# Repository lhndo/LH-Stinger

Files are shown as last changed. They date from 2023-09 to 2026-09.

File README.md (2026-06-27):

<p align="center">
  <p align="center">
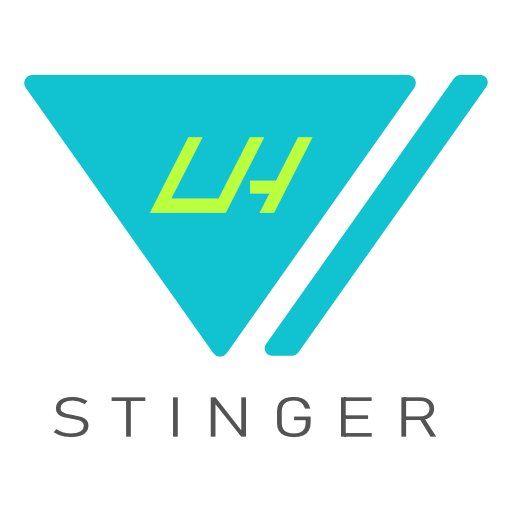
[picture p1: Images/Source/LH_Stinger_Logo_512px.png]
   
  </p>
	<h1 align="center"><b>LH Stinger</b></h1>
	<p align="center"> <strong>
		A no-compromise cartesian 3D Printer designed for speed and precision, created as a long-lasting platform for those who like to push quality and speed to the extreme.  </strong>
    <br />
    <br />
        <br />
    <i>~ A community-driven project ~ </i>
    <br /> 
    <br />
      
    <br />
</a>
  </p>
</p>

<br>

Image of LH Stinger 3D Printer Front View  

<br>

  
Status: **V1.0**  

<br>

## Sponsors

JLCPCB (https://flexheater.jlcpcb.com/?from=LH_STINGER)
  
   Sponsored by [JLCPCB Flexible Heaters](https://flexheater.jlcpcb.com/?from=LH_STINGER) - **Custom Flex Heaters for Your Build**
<br>

## Contents

- [Features](#features)
- [Kits - BOM](#kits---bom)
- [Resources](#resources)
- [Assembly Instructions](#assembly-instructions)
- [Addons](#addons)
- [Contact](#contact)
- [Credits](#credits)
- [Supporters](#supporters)
- [License](#license)

<br>

## Features
_**(at BOM Spec)**_
<br>

- Cross Frame design focused on stiffness and stability with a low center of gravity
- Streamlined frame assembly consisting of only six extrusions
- Lightweight bed carriage assembly with carbon fiber components
- AWD stepper configuration for the Y-axis
  - Optional conversion for X-axis AWD setup
- 235 x 235 x 200 mm maximum build volume (easily expandable to other sizes)
  - (200 mm)^2 [Carbon Fiber Bed](/DXF) for high-speed setup
  - (235 mm)^2 bed support for a larger volume
- Optimized for daily print speeds of 400-600 mm/s with 20.000 mm/s^2 acceleration ([Test A](https://www.youtube.com/watch?v=bxNQv3xVFXA&)) ([Test B](https://www.youtube.com/watch?v=mh0rmYptH-0)) ([Test C](https://www.youtube.com/watch?v=cDipS-Msi5c))
- Motion system capable of 1.000 mm/s speed with 100.000 mm/s^2 acceleration ([Test](https://www.youtube.com/watch?v=Xajs2mky6ZU))
- Maximum volumetric flow rate: ~55-60 mm^3/s ([Test A](https://www.youtube.com/watch?v=K3M1EXKJzKs)) ([Test B](https://www.youtube.com/shorts/JorOoNuft90))
- Built using 30 series T-slotted extrusions with parts up to 3090
- All bracket assembly
- Genuine high-quality motion system components ([BOM](https://docs.google.com/spreadsheets/d/1s8ulLfThmbuy1G_40MvkXXL2oVx9PZhvpAY9hMxqYbg/edit?usp=drive_link))
- Entire motion system based on high preload MGN12H linear guide rails
- Fully belt-driven with minimal belt paths
- 9mm 2GT belt in symmetrical configuration for the Y-axis
- 6mm 2GT belts for the rest of the axis
- Independent Z stepper motors with Z Tilt capability for the X-axis
- Lightweight dual plate [Carbon Fiber Bed Carriage](/DXF) with integrated tensioner and compatible with different bed sizes and carriage configurations
- Rigid carbon fiber bed mount
- Lightweight Polyimide flex PCB 200W [Bed Heater](/PCB/PI%20Bed%20Heater%20-%20200mm)
- Double shear shaft supports for Y and X axis steppers
- High torque LDO-42STH48-2504AC stepper motors supplied with 36V for the X and Y-axis
- Dual power supply supporting 24V and 36V power standards (easily configurable for 48V)
- Driven by the Octopus Pro 1.1 board with TMC2240 drivers
- Running [Klipper](https://github.com/Klipper3d/klipper)/[Kalico](https://github.com/KalicoCrew/kalico) firmware
- Fully featured Klipper [Configuration](/Config/Klipper_Config) and [Slicer Profiles](/Config/Klipper_Config#slicers) available
- Easily serviceable [External electronic box](https://github.com/lhndo/LH-Stinger/wiki/Build-Log#electronic-box-design) with good airflow, and support for multiple power supplies, SSRs, RPi and large controller boards.
- Good cable management with a quick disconnect [Breakout Board](/PCB/LHS%20Breakbeat) between the printer and ebox
- Toolhead based on the Dragon HF hotend and HF extender
  - Alternate hotends supported: Dragon UHF, Ace, Mellow NF-Crazy-Volcano HF, Rapido, Goliath ([User Mods](/User_Mods/Toolhead/))
- LDO Orbiter 2.5 direct drive extruder
  - Sherpa Mini supported ([User Mods](/User_Mods/Printer))
- Dual 5015 fan setup for part cooling
- Dual [AUX cooling modules](/CAD/Aux%20Fan) based on 9733 blower fans providing 64 CFM of auxiliary cooling
- Adopts the [Annex Engineering Quickdraw Probe](https://github.com/Annex-Engineering/Quickdraw_Probe)
	- Zero Y offset probe placement for no gantry twist deviation
	- Full bed probe coverage
- Minimalistic [printed part design](/STL) focused on strength and easy printability
- Printed in ASA, providing high temperature resistance
- Easily enclosed, with the main electronic components outside of the build chamber.
  - The (200 mm)^2 bed configuration can be fully enclose up to the frame bounding box, with no extra space needed for the bed movement. ([Dimensions](https://github.com/lhndo/LH-Stinger/wiki/Dimensions))

<br>

**Resonance Tests:**<br>
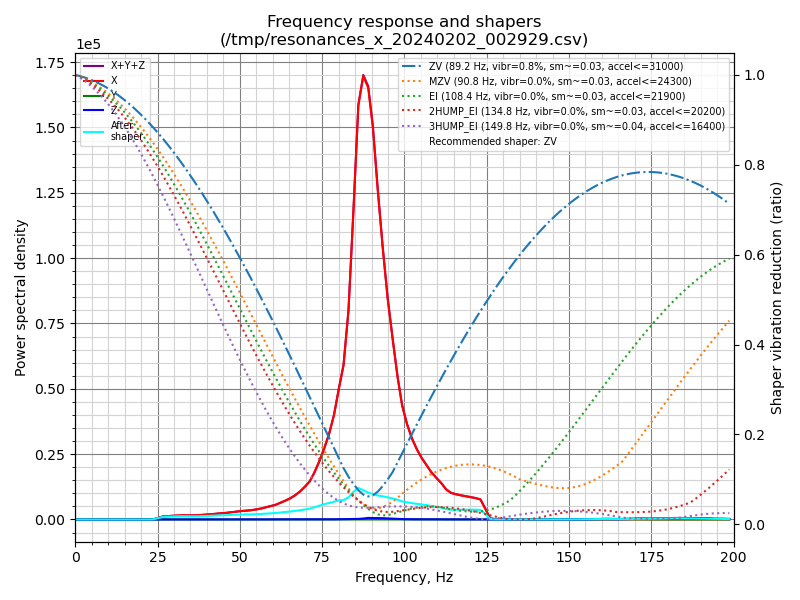
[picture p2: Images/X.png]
Resonance Test X
<br>
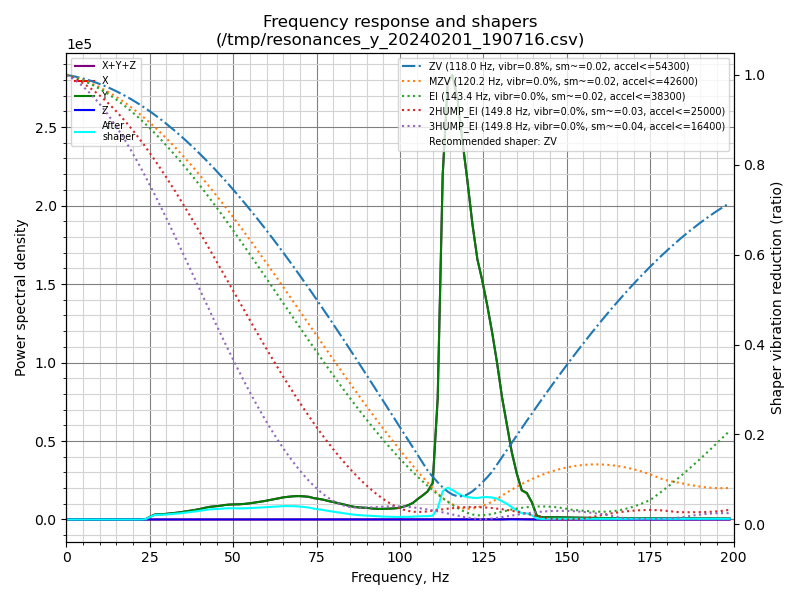
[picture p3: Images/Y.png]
Resonance Test Y
<br>

<br>

## Kits - BOM

* This project can be self-sourced by following the [**BOM Guide**](https://docs.google.com/spreadsheets/d/1s8ulLfThmbuy1G_40MvkXXL2oVx9PZhvpAY9hMxqYbg/).  

* An official upgraded **LH Stinger - Rev2 Kit** is produced and sold by **[FYSETC](https://www.fysetc.com/products/lh-stinger-3d-printer-kit)**.

Fysetc LH Stinger Rev2 Kit (https://www.fysetc.com/products/lh-stinger-3d-printer-kit)<br>

### Kit Highlights:

* Phaetus Dragon UHF - Hotend
* FYSETC Sherpa Mini - All Metal - CNC Extruder
* MGN 12H Z1 Preload Linear Rails
* FYSETC Spider V3.0 H7 (550Mhz) High Voltage board 
* 48V Power with TMC5160 Drivers (AWD Y, X Axis)
* High Torque 2.5A 580mN.m Stepper Motors with 30mm shafts for double shear support
* Delta (48V) and Meanwell (24V) PSUs
* Carbon Fiber Bed with Pre-applied PI Heater and Pre-epoxied CF Carriage Assembly
* LHS Breakbeat distribution board and wiring harness

**You require**: The **Printed Parts** and a **BTT Pi V1.2** or **Raspberry Pi** SBC (Klipper Host)
<br>

[**Fysetc - LH Stinger - Kit**](https://www.fysetc.com/products/lh-stinger-3d-printer-kit)  
  
Use the code **FYSBKSALELH** for a total of **$699**. Free shipping directly from US/EU.  
A portion of every kit sale goes towards supporting the project! :purple_heart:  

<br>

## Resources
<br>

- [**Assembly Guide**](https://github.com/lhndo/LH-Stinger/wiki/)
- [STL Files and Printing Instructions](STL/)  
- [CAD Source Files ](CAD/)
- [Klipper Configuration ](Config/Klipper_Config) 
- [Build Log](https://github.com/lhndo/LH-Stinger/wiki/Build-Log)
- [Videos](https://www.youtube.com/channel/UCPD2Ai4b49gVoCFSGFWoSdw) 

<br>

## Assembly Instructions 

* The [LH Stinger Wiki](https://github.com/lhndo/LH-Stinger/wiki) is a regularly updated and intended to serve as your primary point of reference during the build  

* The main body of documentation can be found in the [**Assembly Guide**](https://github.com/lhndo/LH-Stinger/wiki/Assembly-Guide)  

<br>

*For additional support please join us on the [LH Stinger Discord](https://discord.gg/EzssCfnEDS)*

<br>

## Addons

- [**LHS Pico MMU**](https://github.com/lhndo/LH-Stinger/wiki/Pico-MMU)  

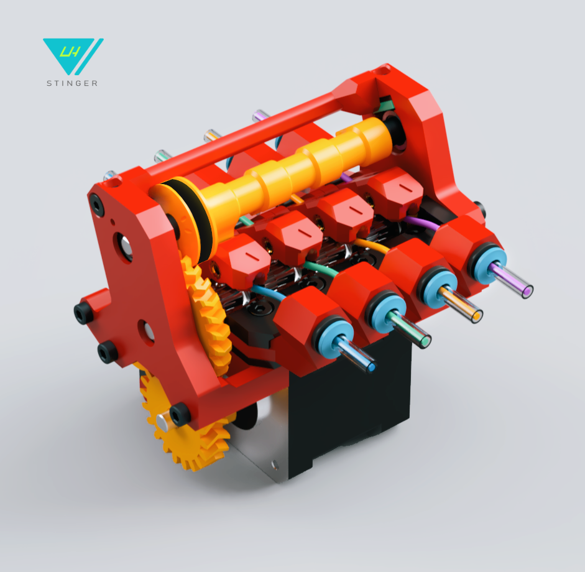
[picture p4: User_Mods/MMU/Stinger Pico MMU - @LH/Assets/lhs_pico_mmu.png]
LH Stinger - LHS - Pico MMU


- **Enclosure** *(In progress)* 
  *by zwirbel*

<br>

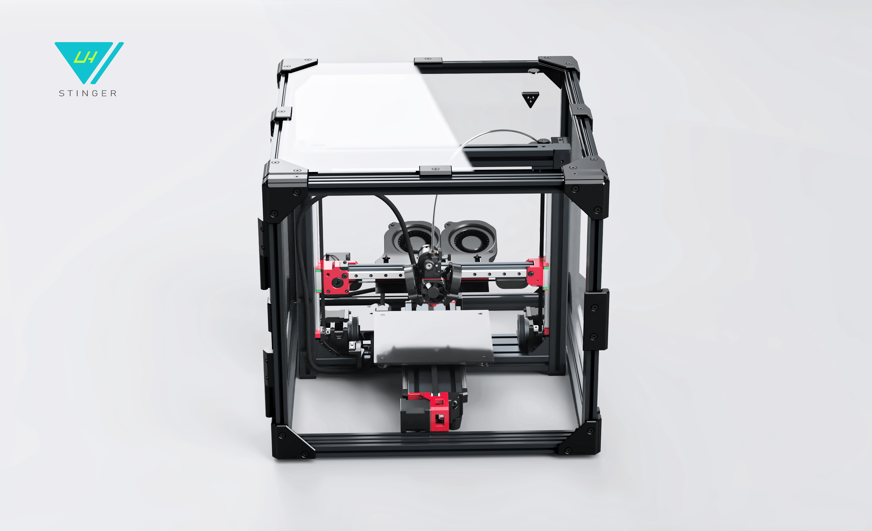
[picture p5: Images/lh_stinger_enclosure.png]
LH Stinger Enclosure
  

<br>

- An extensive range of [**community mods**]((/User_Mods)) available

<br>

## Contact

lemurshaze @ gmail.com  
@LH on [LH Stinger Discord](https://discord.gg/EzssCfnEDS)
<br>

## Credits

<br>

**Thanks to everyone in the LH Stinger community who supported the project, contributed in any form, or provided feedback! :purple_heart:**

<br>

_Inspired by the [Annex Engineering](https://github.com/Annex-Engineering) team and [community](https://discord.com/invite/MzTR3zE), along with the [Klipper community](https://discord.klipper3d.org), [RatRig](https://ratrig.com/) and all the crazy people that continue to push bed slingers to their limits. :purple_heart:_

-Toolhead evolved from an amazing design by [Dalegaard](https://github.com/dalegaard)  
-Silicon sock mold based on [Renátó Kulman](https://www.printables.com/@RenatoKulman)  
-Wago 221 mounts by [fns720](https://www.printables.com/@fns720)  
-SSR protection cover based on [Technoturk](https://www.printables.com/@Technoturk_377911)  
-3030 extrusion Cable clip based on [Arthur_C](https://www.printables.com/@Arthur_C_428094)  
-3030 t-nut clip based on [John_S](https://www.printables.com/@JohnS)  
<br>

## Supporters

<br>

*Special thanks to those who donated to this project throughout its development!* :purple_heart:  

**djezo888. Fen, Budz, techb0i, PinGZ, abstractFlo, BeccaK, Steven @crydteam, Robin @crydteam, Fred Bernton, Mawoka, rmxbit, Mcclane, malar6606, EMMY BEAR 3D, Killa_Prints, Michel, vr6deezy, Ajax240, Zemlos01, popster, Dan, Sibert, Ultracopa, yoske, Arjun, iKuro**  

If you would like to give your support, please use the link below:



<br>

## License

This work is licensed under a [Creative Commons (4.0 International License)  ](https://creativecommons.org/licenses/by-nc-sa/4.0/)  
[**Attribution—Noncommercial—Share Alike**](LICENSE.md)  

[][cc-by-nc-sa] [][l2] [][l5] 

[s1]: https://img.shields.io/badge/Buy%20Me%20a%20Coffeee-d3dsds?logo=ko-fi&logoColor=white&labelColor=red&color=red
[l1]: https://ko-fi.com/lh_eng
[s2]: https://img.shields.io/badge/Discord-asdsadsa?logo=discord&logoColor=white&color=5865F2
[l2]: https://discord.gg/EzssCfnEDS
[s5]: https://img.shields.io/badge/Youtube-8A2323443?logo=youtube&logoColor=red&color=white
[l5]: https://www.youtube.com/@LemurHaze

[cc-by-nc-sa]: http://creativecommons.org/licenses/by-nc-sa/4.0/
[cc-by-nc-sa-image]: https://licensebuttons.net/l/by-nc-sa/4.0/88x31.png
[cc-by-nc-sa-shield]: https://img.shields.io/badge/License-CC%20BY--NC--SA%204.0-lightgrey.svg

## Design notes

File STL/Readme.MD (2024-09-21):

[:arrow_double_down: Download Folder](https://download-directory.github.io/?url=https%3A%2F%2Fgithub.com%2Flhndo%2FLH-Stinger%2Ftree%2Fmain%2FSTL)

## Naming Conventions

Filename Example: **AC** Y Stepper Mount A **SUP x2**.stl

> **AC** - Accent color part  
> **SUP** - Supports needed  
> **x2** - Number of part copies required

<br>

## Print Settings

### Filament Options  
&nbsp;&nbsp;&nbsp;&nbsp; **Printer**: ASA, PC (CF, GF)  
&nbsp;&nbsp;&nbsp;&nbsp;&nbsp;**Ebox, Breakout**:  PETG, ASA, ABS (Flame-retardant Filaments)  

### Slice Setings

&nbsp;**Printer Parts:**  

&nbsp;&nbsp;&nbsp;&nbsp;Nozzle Size: 0.4 or 0.5 mm  
&nbsp;&nbsp;&nbsp;&nbsp;Layer Height: 0.2  
&nbsp;&nbsp;&nbsp;&nbsp;Line Width: 0.4  (0.5mm)  
&nbsp;&nbsp;&nbsp;&nbsp;Perimeters: 4  
&nbsp;&nbsp;&nbsp;&nbsp;Top / Bottom Layers: 6/5  
&nbsp;&nbsp;&nbsp;&nbsp;Infill Density: 40% minimum  
&nbsp;&nbsp;&nbsp;&nbsp;Infill Type: 3D Honeycomb, Gyroid, Cubic 

&nbsp;**Ebox, Breakout, Other Parts:**  
&nbsp;&nbsp;&nbsp;&nbsp;At your discretion  

<br>

>**Note: If printing the STL files individually in another slicer,  please install Orca Slicer and reference the orientation and supports used in the provided ready made 3mf plates.**

<br>

## Filament Amounts

Printer: 260g  
Printer Accents: 210g

Aux Fan: 127g  
Aux Fan Accents: 44g

Breakout: 97g

Ebox: 729g  
Ebox Accents: 49g

Other Parts: 204g  

<br>

## Assemblies

Files containing all the parts organized by plates are available in the .3mf format for [Orca Slicer](https://github.com/SoftFever/OrcaSlicer)

**Printer Parts:**  <br>

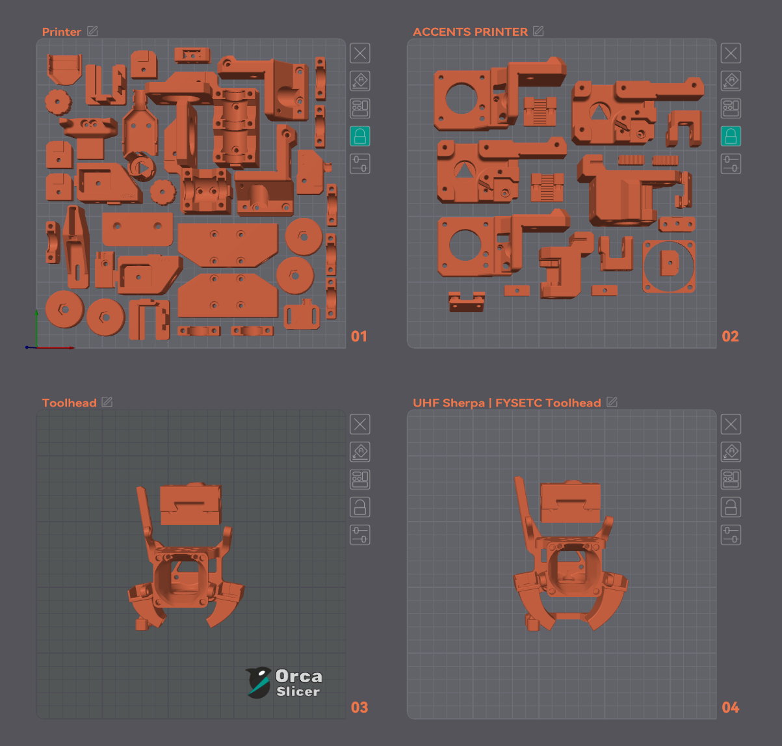
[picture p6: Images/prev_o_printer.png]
  
<br>

**Aux Fan Parts:**  <br>

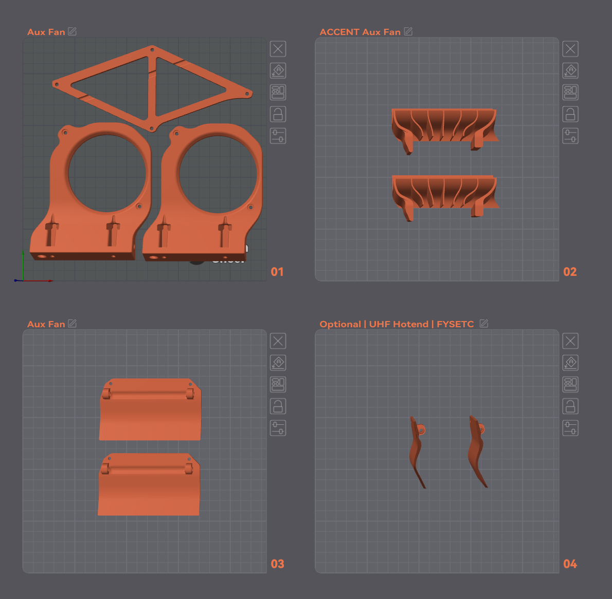
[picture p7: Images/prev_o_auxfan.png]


<br>

**Ebox Parts:**  <br>

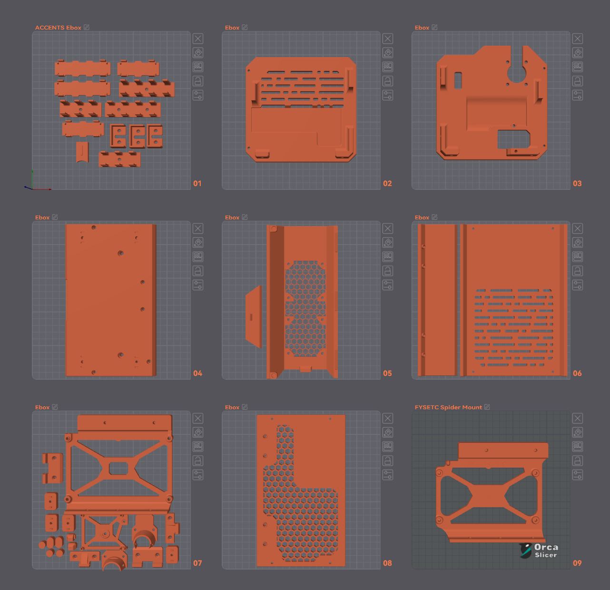
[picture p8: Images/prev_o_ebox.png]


<br>

**Breakout Box Parts:**  <br>

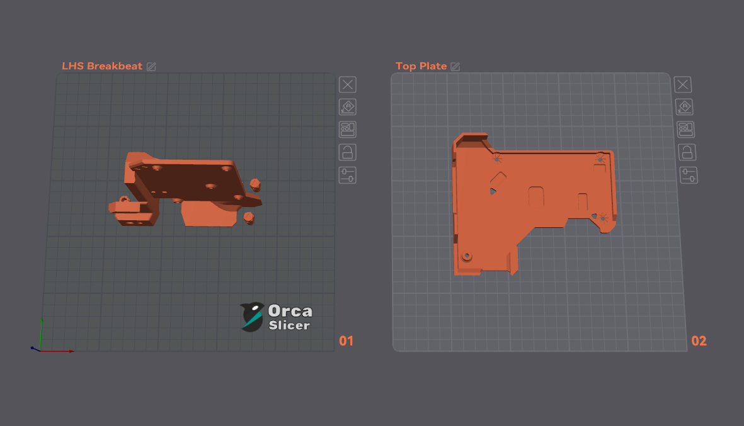
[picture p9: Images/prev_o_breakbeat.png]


<br>

**Other Parts:**  <br>

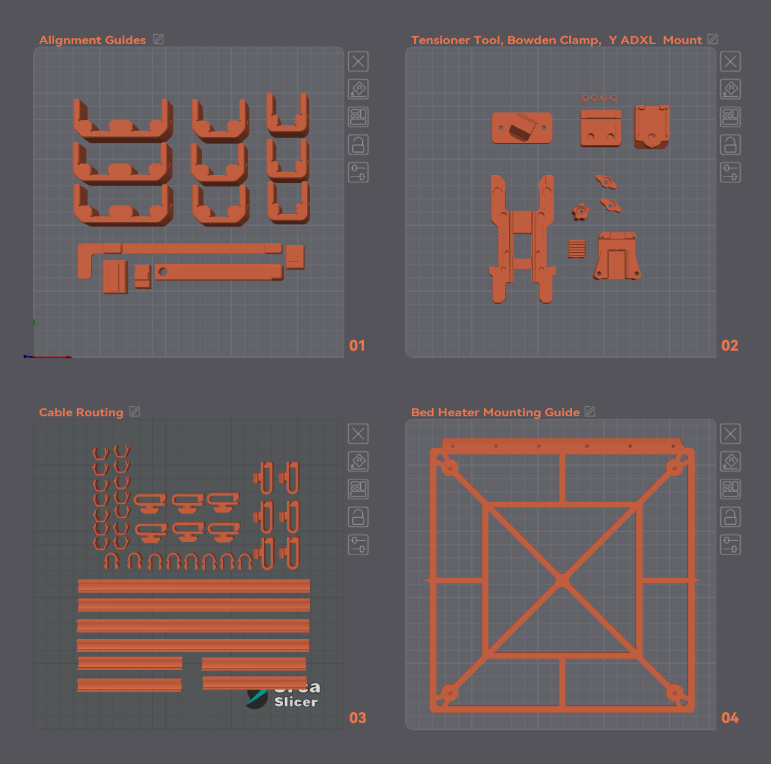
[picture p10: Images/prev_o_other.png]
  
<br>

## Quickdraw

Details about the Quickdraw probe can be found on the [Annex Engineering Git](https://github.com/Annex-Engineering/Quickdraw_Probe/tree/main)  
The file required for building the probe is **omron_d2f-5_microswitch_probe_body_x1_rev3.STL**  
from: https://github.com/Annex-Engineering/Quickdraw_Probe/tree/main/STLs/Release_1

Assembly tips can be found in the [Toolhead Guide - Probe](https://github.com/lhndo/LH-Stinger/wiki/Toolhead#probe) section.  

Note: The dock detection feature is not required and not accounted for in the dock stl.

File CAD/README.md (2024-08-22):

## CAD

The project was built in Fusion 360, and those files are preferred as the primary choice for consulting the assembly.  
They are packed into f3z files, which maintain links/instances to all components and sub-assemblies. This way it is easier to make modifications by third parties and keep track of the changes for future integration.  
It is advised to create a folder inside your Fusion workspace in which to import the f3z.  
<br>
STEP files are provided for compatibility with other CAD software. 

<br>

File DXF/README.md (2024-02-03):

## CFRP Plates - Temperature Deflection Test

<br>

* Temperature deflection test on four 200mmx200mm CFRP Plates sourced from different vendors.  

<br>

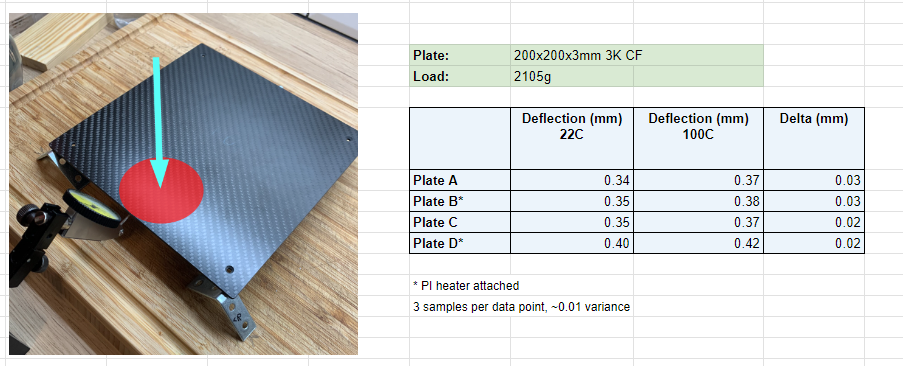
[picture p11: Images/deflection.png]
Deflection Test
    

<br>

* Deflection comparison against the Ender 3 4mm aluminium carriage.  

<br>

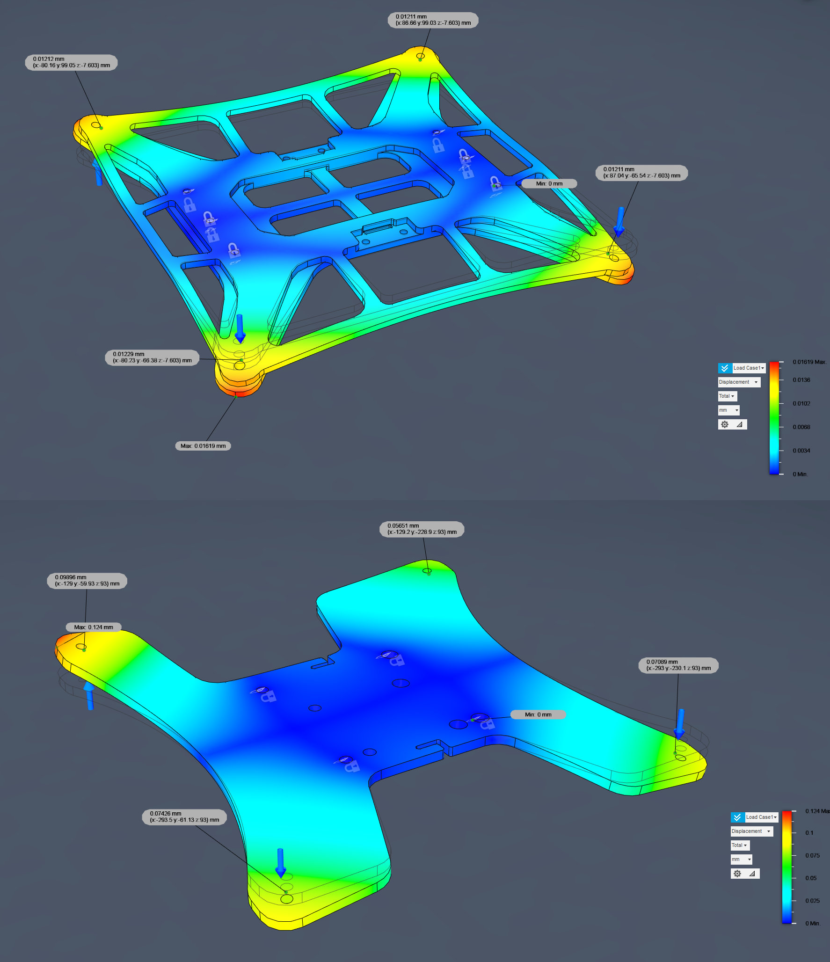
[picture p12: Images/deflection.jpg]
Deflection Test
    

<br>

* Bed mesh flatness range at ambient and temp.

<br>

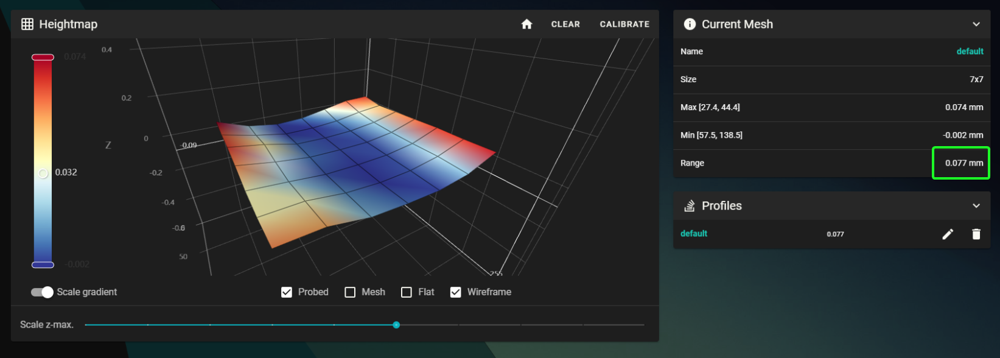
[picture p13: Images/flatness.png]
    

<br>

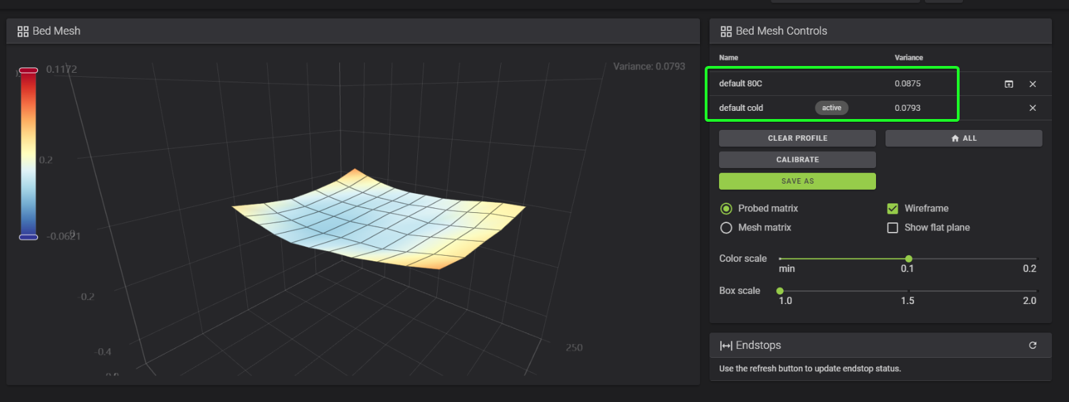
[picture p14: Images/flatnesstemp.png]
    

<br>

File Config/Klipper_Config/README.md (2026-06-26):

[:arrow_double_down: Download Folder](https://download-directory.github.io/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)

<br>

### LH Stinger - Software Installation Guide

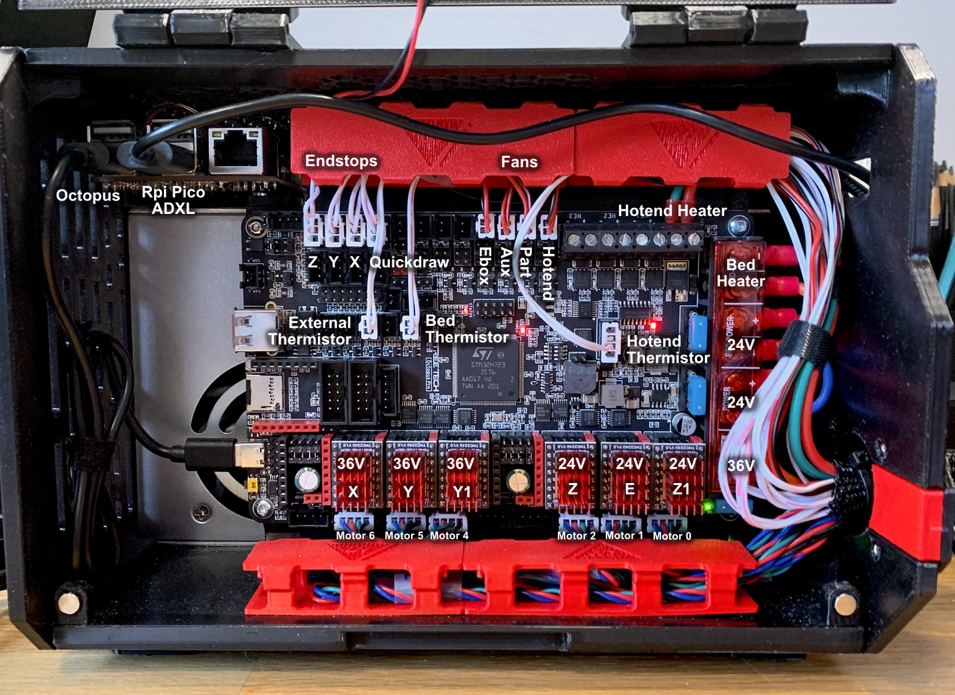
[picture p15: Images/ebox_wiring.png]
Ebox Wiring
  

## Contents:
<!--ts-->

- [Prerequisites](#prerequisites)
  - [Host](#host)
    - [BTT PI 1.2](#btt-pi-12)
    - [Raspberry PI](#raspberry-pi)
  - [SSH](#ssh)
  - [KIAUH](#kiauh)
  - [Firmware](#firmware)
    - [Octopus PRO](#octopus-pro)
    - [FYSETC Spider 3 H7](#fysetc-spider-3-h7)
- [Configuration](#configuration)
  - [Klipper](#klipper)
  - [XZ Dockable Probe](#xz-dockable-probe)
  - [Gcode Shell Command](#gcode-shell-command)
  - [ResHelper](#reshelper)
  - [Resonance Holder](#resonance-holder)
- [Themes](#themes)
- [Moonraker](#moonraker)
    - [Power Relay (Optional)](#power-relay-optional)
- [Slicers](#slicers)
  - [Bed Origin](#bed-origin)
  - [Slicer Start Gcode](#slicer-start-gcode)
    - [Orca Slicer](#orca-slicer)
    - [Prusa Slicer](#prusa-slicer)
- [Support](#support)
<!--te-->
<br>

# Prerequisites

<br>

:blue_book: It is recommended to perform the installation in the order listed below.
<br>

## Host

### BTT PI 1.2
Download the OS image: https://github.com/bigtreetech/CB1/releases (Choose **CB1_Debian11_minimal** )  
Use [Balena Etcher](https://etcher.balena.io/) to burn the image onto the PI SD Card.

**Video:** [BTT Pi Overview & Installation Guide](https://www.youtube.com/watch?v=xBpkeKKwu48)

**WIFI configuration:**
1. Re-insert the SD card into your computer, open the **BOOT** drive and add your Wi-Fi credentials to **system.cfg**

<br>

### Raspberry PI

Read the following guide to install the **MainsailOS**  
https://docs-os.mainsail.xyz/getting-started/raspberry-pi-os-based

**WIFI configuration:**
1. Set up your WIFI connection in the **Raspberry Pi Imager** before burning the image.  
2. Re-insert the SD card into your computer, open the **BOOT** drive and add your Wi-Fi credentials to **mainsailos-wpa-supplicant.txt**

<br>

## SSH

#### Tools
To communicate with your **Host** you will need a **SSH** and an **SFTP** client  
The easiest way is to install [**MobaXterm**](https://mobaxterm.mobatek.net/features.html) which provides both of these functions. 

#### IP

  If you pre-configured your SSID and WIFI Password correctly, or if you connect though a ethernet cable, you can try the following ways to find your Klipper IP address:  
     
  A. Open your  your ROUTER dashboard and look at the device list  
  B. Open command prompt and run : `ping mainsailos.local -4` (Rraspberry Pi)  
  C. Install and run [Angry IP Scanner](https://angryip.org)   

<br>

## KIAUH
**KIAUH** is a rich featured script that makes it extremely easy to perform any Klipper related software installation, setup and firmware flashing starting from a bare OS.  
**This should be the first thing to install after finishing your OS installation.**

https://github.com/dw-0/kiauh/tree/master  

KIAUH installation:

1. Install KIAUH
```
sudo apt-get install git -y
cd ~ && git clone https://github.com/dw-0/kiauh.git
```
2. Run KIAUH and select mode **4** (No to using the Alpha version)
   
   `~/kiauh/kiauh.sh`

<br>

From **KIAUH** install:
- **Klipper** (Python 3.x)
- **Moonraker**
- **Mainsail**

<br>

## Firmware

:bulb: The firmware setup process can be easily done directly from **KIAUH**

### Octopus PRO 
Follow the steps starting from "Build your own firmware" and make sure to choose the appropriate settings for your own MCU type (The BOM recommendation is the Octopus Pro V1.1 with the H723 chip)

These are also mentioned in the header of **printer.cfg** file above.

https://github.com/bigtreetech/BIGTREETECH-OCTOPUS-V1.0/tree/master/Firmware/Klipper#build-firmware-image  
<br>

### FYSETC Spider 3 H7 

For the FYSETC board included in the LH Stinger kits please follow the following firmware flashing guide:

https://github.com/lhndo/LH-Stinger/wiki/FYSETC-S3-H7-Firmware-Guide

<br>
<br>

# Configuration

<br>

## Klipper

To set up the required Klipper LH Stinger configuration files please follow these steps:

* Download the configuration files onto the Raspberry/BTT Pi by running the following commands though **SSH**

```
rm -rf ~/lhs && git clone --filter=blob:none --sparse https://github.com/lhndo/LH-Stinger.git ~/lhs && cd ~/lhs
git sparse-checkout init --cone
git sparse-checkout set Config/Mainsail_Theme/
git sparse-checkout add Config/Klipper_Config/
git sparse-checkout add KITS/FYSETC/Klipper_Config_FYSETC/
cp -r ~/printer_data/config/ ~/printer_data/config/backup/
mkdir -p ~/printer_data/config/.theme
cp -r ~/lhs/Config/Mainsail_Theme/* ~/printer_data/config/.theme/
```

<br>

* Copy the configuration files to their correct location with the following commands:

<br>

### :large_blue_diamond: Option **A** : **LH Stinger BOM Build - BTT Octopus Pro v1.2** 

```
cp -r ~/lhs/Config/Klipper_Config/* ~/printer_data/config/
systemctl restart klipper
```
<br>

### :large_orange_diamond: Option **B** : **FYSETC - LH Stinger - Spider H7** 

```
cp -r ~/lhs/KITS/FYSETC/Klipper_Config_FYSETC/* ~/printer_data/config/
systemctl restart klipper
```

<br>

For more information please consult:  
[Klipper Configuration Reference](https://www.klipper3d.org/Config_Reference.html)  
[Ebox Guide](https://github.com/lhndo/LH-Stinger/wiki/Ebox)  
[Breakout Guide](https://github.com/lhndo/LH-Stinger/wiki/Breakout-Box)  
[FYSETC Kit Guide](https://github.com/lhndo/LH-Stinger/wiki/FYSETC-Kit)  

<br>
<br>

# Klipper Modules
:children_crossing: **The klipper modules below are required for the LH Stinger setup**

<br>

## XZ Dockable Probe

The XZ Dockable Probe module incorporates some unique homing features and is required for the QuickDraw probe.

:children_crossing: If running the latest Klipper version, you will need to temporarily drop back a few changes due to recent API changes.  
To do so, run the following in the SSH console:

```
cd ~/klipper
git checkout 4cc47cf
sudo systemctl restart klipper
```

To install the probe module, run:

<pre><code>cd ~/klipper/klippy/extras/
wget https://raw.githubusercontent.com/lhndo/klipper/red/klippy/extras/xz_dockable_probe.py
cd ../..
echo "klippy/extras/xz_dockable_probe.py" >> .git/info/exclude
git update-index --assume-unchanged klippy/extras/xz_dockable_probe.py > /dev/null 2>&1
</code></pre>

by [Dalegaard](https://github.com/dalegaard) and [Churls](https://github.com/churls5495/Annex-Engineering_User_Mods/tree/main/Extruders/Sherpa_Mini/Toolheads/Churls-Stiffy_E3)

<br>

## Gcode Shell Command

**Installation:**
```
cd ~/klipper/klippy/extras/
rm gcode_shell_command.py
wget https://raw.githubusercontent.com/KalicoCrew/kalico/refs/heads/main/klippy/extras/gcode_shell_command.py
cd ../..
echo "klippy/extras/gcode_shell_command.py" >> .git/info/exclude
git update-index --assume-unchanged klippy/extras/gcode_shell_command.py > /dev/null 2>&1
```

## ResHelper

ResHelper is an utility script that simplifies and streamlines the resonance testing process. 
Follow the installation steps from the following link or the code commands below.  
https://github.com/lhndo/ResHelper

<br>

**Installation:**
```
cd ~ && git clone https://github.com/lhndo/ResHelper.git
cd ResHelper
./install.sh
```

<br>

## Resonance Holder

For debugging resonance peaks 

```
cd ~/klipper/klippy/extras/
wget https://raw.githubusercontent.com/lhndo/danger-klipper/bleeding-edge-v2/klippy/plugins/resonance_holder.py
cd ../..
echo "klippy/extras/resonance_holder.py" >> .git/info/exclude
git update-index --assume-unchanged klippy/extras/resonance_holder.py > /dev/null 2>&1
systemctl restart klipper
```
**Usage:**
Uncomment **[resonance_holder]** in **printer.cfg** and use the [VIBRATION TEST](https://github.com/lhndo/LH-Stinger/wiki/Macros#vibration-test) macro for testing.

<br>
<br>

# Themes

[**Mainsail**](https://github.com/lhndo/LH-Stinger/tree/main/Config/Mainsail_Theme)
[**Fluidd**](https://github.com/lhndo/LH-Stinger/tree/main/Config/Fluidd_Theme)

<br>

# Moonraker 

### Power Relay (Optional)
If using a Power Relay to control the AC supply to the Ebox, then add the following section to your **moonraker.conf** .  
Note: The PI should be on its own independent power supply. 

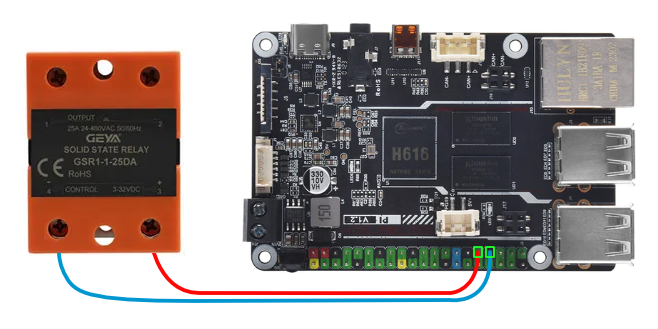
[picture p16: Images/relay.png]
Relay


<pre><code>[power Printer]
type: gpio
pin: gpiochip0/gpio262
off_when_shutdown: True
initial_state: off
restart_klipper_when_powered: True
</code></pre>

<br>

* **BTT Pi 1.2** connect though SSH, run the following commands and restart the Pi:

```
sudo sh -c 'echo "# udev rules for gpio port access through libgpiod
SUBSYSTEM==\"gpio\", KERNEL==\"gpiochip[0-4]\", GROUP=\"biqu\", MODE=\"0660\"" > /etc/udev/rules.d/60-gpiod.rules'
```
```
sudo udevadm control --reload-rules
sudo udevadm trigger
```

For more information on the **BTT Pi GPIO** pinout please consult this table: https://github.com/bigtreetech/CB1#40-pin-gpio

<br>

# Slicers

### [Orca Slicer 2.4.0](https://github.com/OrcaSlicer/OrcaSlicer/releases) or newer includes the LH Stinger printer and filament profiles.

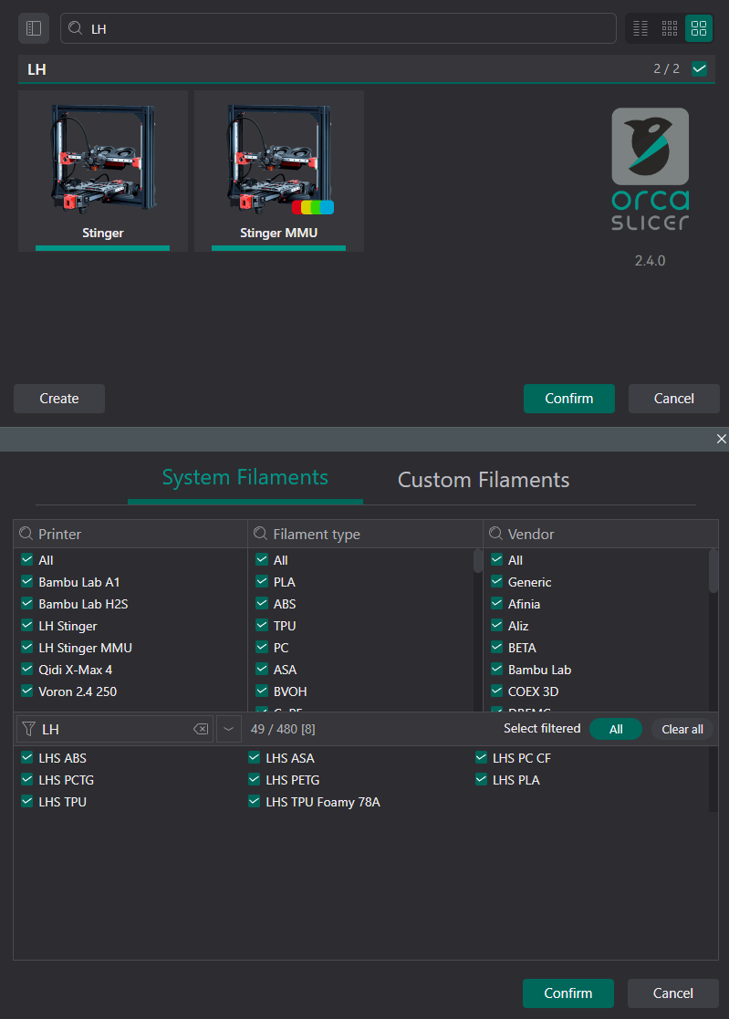
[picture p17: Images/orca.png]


## Bed Origin

***Note: The following settings are included in the provided LH Stinger - Orca Slicer Profiles***  

The printer supports multiple bed sizes. For ease of use, the bed position is defined in the slicer by changing the Origin Offsets, and **not in Klipper's printer.cfg** by changing position_endstop and position_min for X/Y axis.  

Move the nozzle manually to the front left corner of the bed, and note the position, eg. X18 Y38.  
Add those values in the Origin section as negative values. 

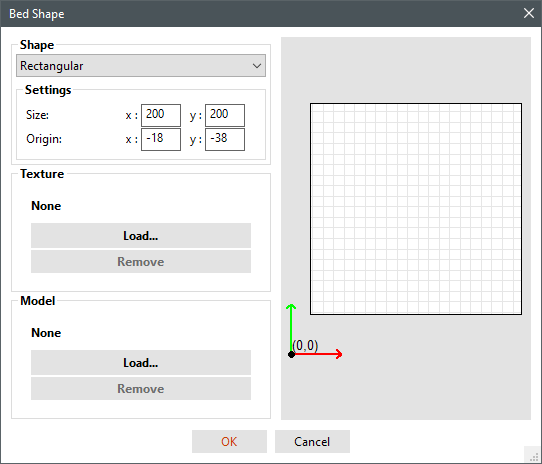
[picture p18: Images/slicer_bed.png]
Slicer Bed Settings


<br>

## Slicer Start Gcode

### Orca Slicer

***Note: The following settings are included in the provided LH Stinger - Orca Slicer Profiles***

Machine Start G-Code:  

`
PRINT_START_LHS BED=[bed_temperature_initial_layer_single] HOTEND=[nozzle_temperature_initial_layer] AUTOMESH=1 AUTOPURGE=1 QUIETMODE={if print_preset =~ /.*Quiet.*/ }1{else}0{endif}
`

Machine End G-Code: 

`PRINT_END`  

<br>

### Prusa Slicer

In Printer Settings > Custom G-Code set:  

Start G-Code:  

`
PRINT_START_LHS BED=[first_layer_bed_temperature] HOTEND=[first_layer_temperature[initial_extruder]] AUTOMESH=1 AUTOPURGE=1 QUIETMODE=0
`

End G-Code: 

`PRINT_END`

<br>

:arrow_forward: For more information please visit: [Wiki>Macros>Slicers](https://github.com/lhndo/LH-Stinger/wiki/Macros#slicers)

<br>

# Support

For support please join the [LH Stinger Discord](https://discord.gg/EzssCfnEDS), or the [Klipper Discord](https://discord.klipper3d.org/)  

<br>

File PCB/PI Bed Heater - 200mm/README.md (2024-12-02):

**Contents:**
- [Specifications](#specifications)
- [Performance](#performance)
- [Installation](#installation)
- [Media](#media)
- [Ordering](#ordering)

<br>

**Disclaimer**

>*This is a DIY (Do-It-Yourself) experimental project. This PCB is provided "as is" without any guarantees or warranty, and is not certified for any commercial or critical applications. Use it at your own risk. 
The creator assumes no liability for damages or injuries resulting from its use, including but not limited to fire, electric shock, personal injury or property damage.*
>*By using this PCB, you agree to the terms of this disclaimer.*

<br>

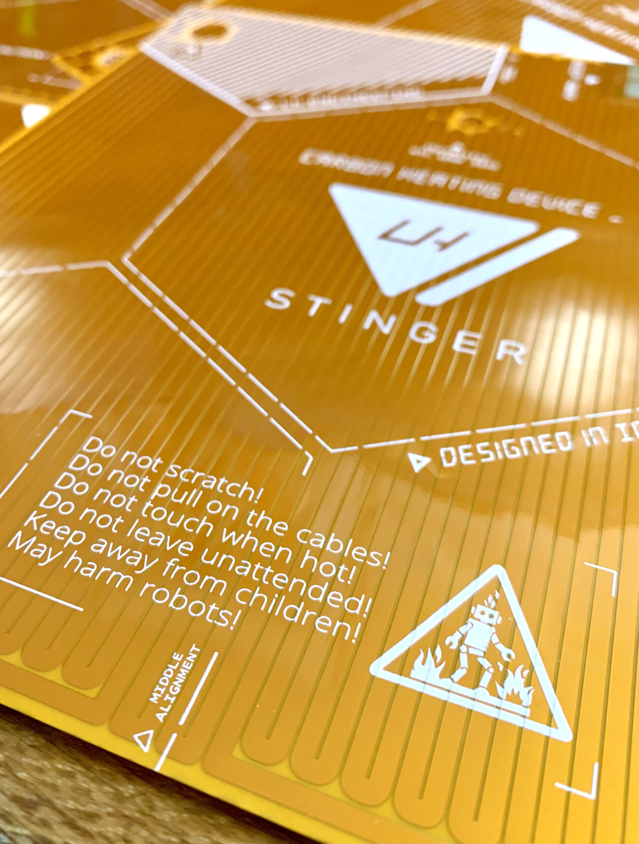
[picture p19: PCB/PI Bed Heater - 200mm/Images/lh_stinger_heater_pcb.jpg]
  

# Specifications  

<br>

_This model is also available for purchase from [Provok3d](https://provok3d.com/product-category/printers/lh-stinger/?v=0a10a0b3e53b&sld=211)_

<br>

**PCB**

- Flex Polyimide Base
- Copper Thickness: 1oz (35 µm)
- Backside Adhesive (Cold Pressed): 3M468MP (Stronger) / 3M90777 (High Temp and easier to apply/remove)
- Silkscreen: White
- Weight: 19g

**Power** 

- Voltage:  24V DC
- Resistance: 2.66 Ohm @ 25C (Please see the included Excel screenshot for calculations)
- Power: 216W @ 25C (+-10%)

**Thermistor** 
- NTC 100K 3950

**Power Cable**

 - 16 AWG Multi-strand Soft Electrical Silicone Cable
 - XT60 female connector
 - Length: 90cm  

**Thermistor Cable**

- PTFE/FEP Wire around 24-26 AWG
- 2 pin JST XH 2.54 female connector
- Length: 90cm  
<br>

>For optimizing your own heater wattage you can use the following calculator. Start with a Trace Width: 2.4mm, Lenght: 13355mm, Thickness: 1oz,   
>https://www.allaboutcircuits.com/tools/trace-resistance-calculator/  

<br>

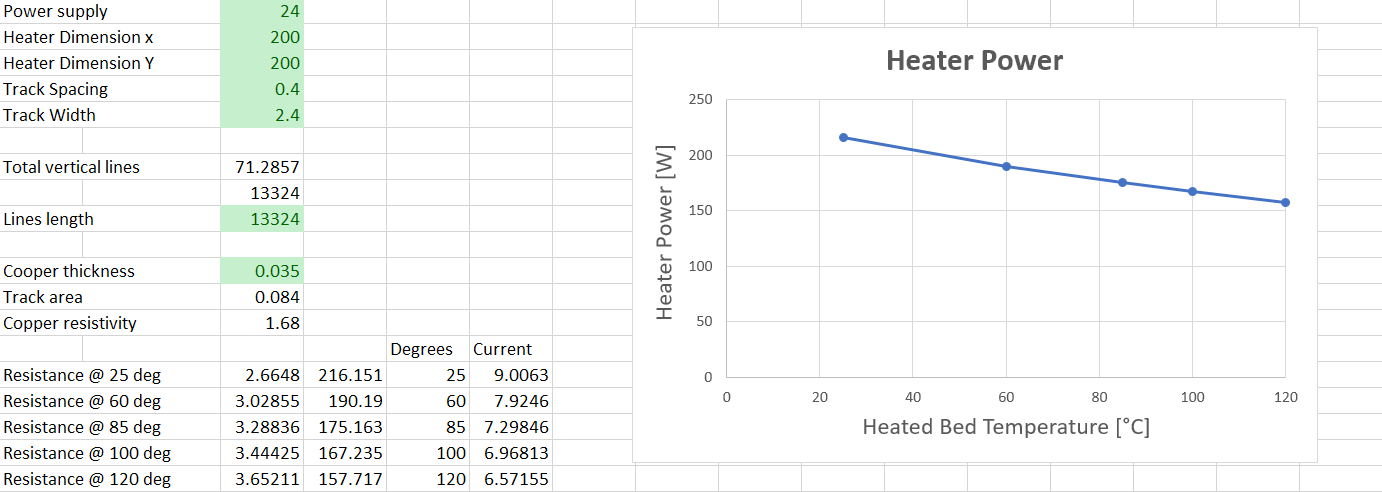
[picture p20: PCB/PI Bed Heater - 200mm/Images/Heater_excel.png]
  

>Designed with the help of [Róbert Lőrincz](https://www.orbiterprojects.com/)  
>[Story Of The Orbitron Heated Bed Design](https://www.orbiterprojects.com/stories/story-of-the-orbitron-heated-bed-design/) 

<br><br><br>

# Performance

<br>

* **Heating time to 110C: 2m 58s**     
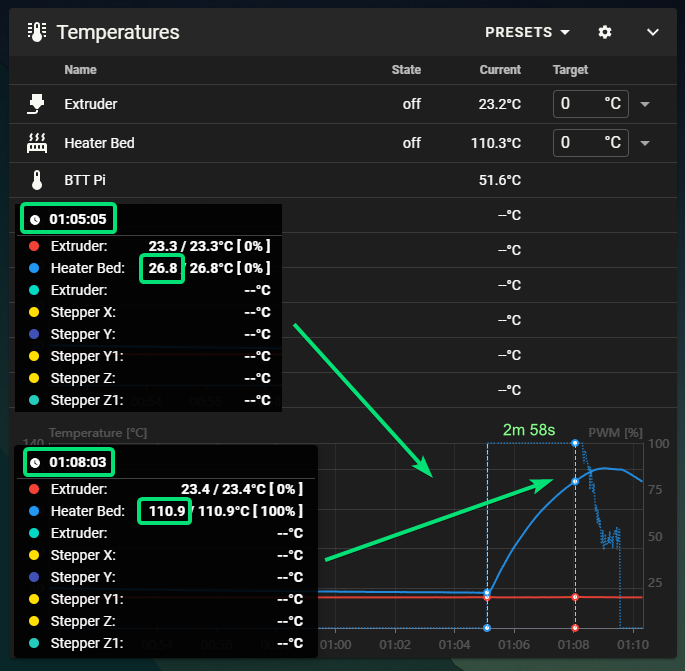
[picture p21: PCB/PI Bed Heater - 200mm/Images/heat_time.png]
  

<br>

* **Bottom thermistor vs top surface thermistor temperature tracking:**      
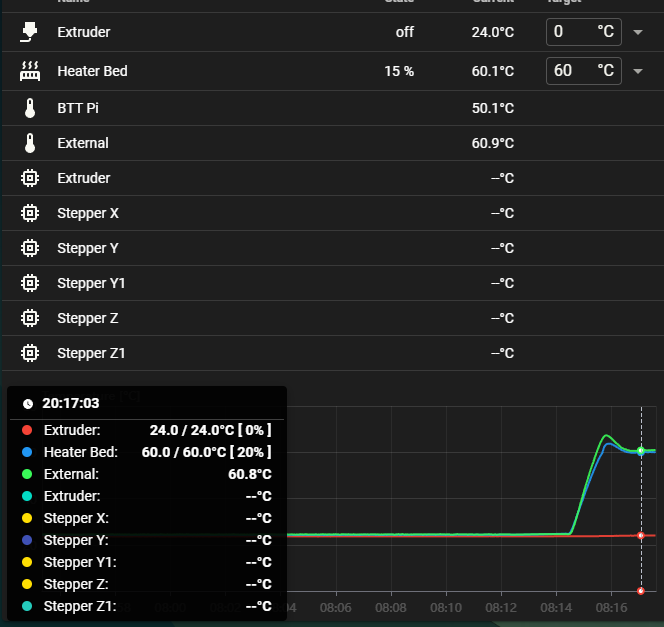
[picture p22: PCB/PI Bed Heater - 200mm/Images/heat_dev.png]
  

<br>

# Installation

Please follow this guide: https://github.com/lhndo/LH-Stinger/wiki/Bed-Heater

<br>

# Ordering

_**[JLCPCB](https://jlcpcb.com) - [OSHWLab](https://oshwlab.com/andrei6/lhs-pi-bed-heater-200x200mm)**_

<br>

1.  Open project from OSHWLab: https://oshwlab.com/andrei6/lhs-pi-bed-heater-200x200mm

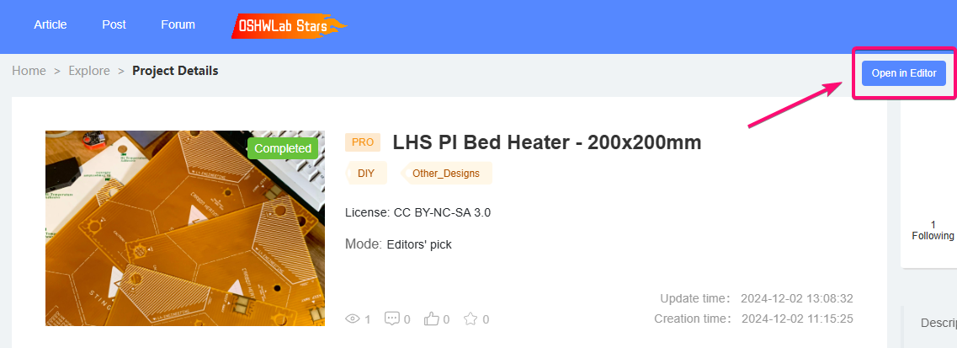
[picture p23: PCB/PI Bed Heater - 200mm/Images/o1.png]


2. Follow the steps below in the online EasyEDA editor:

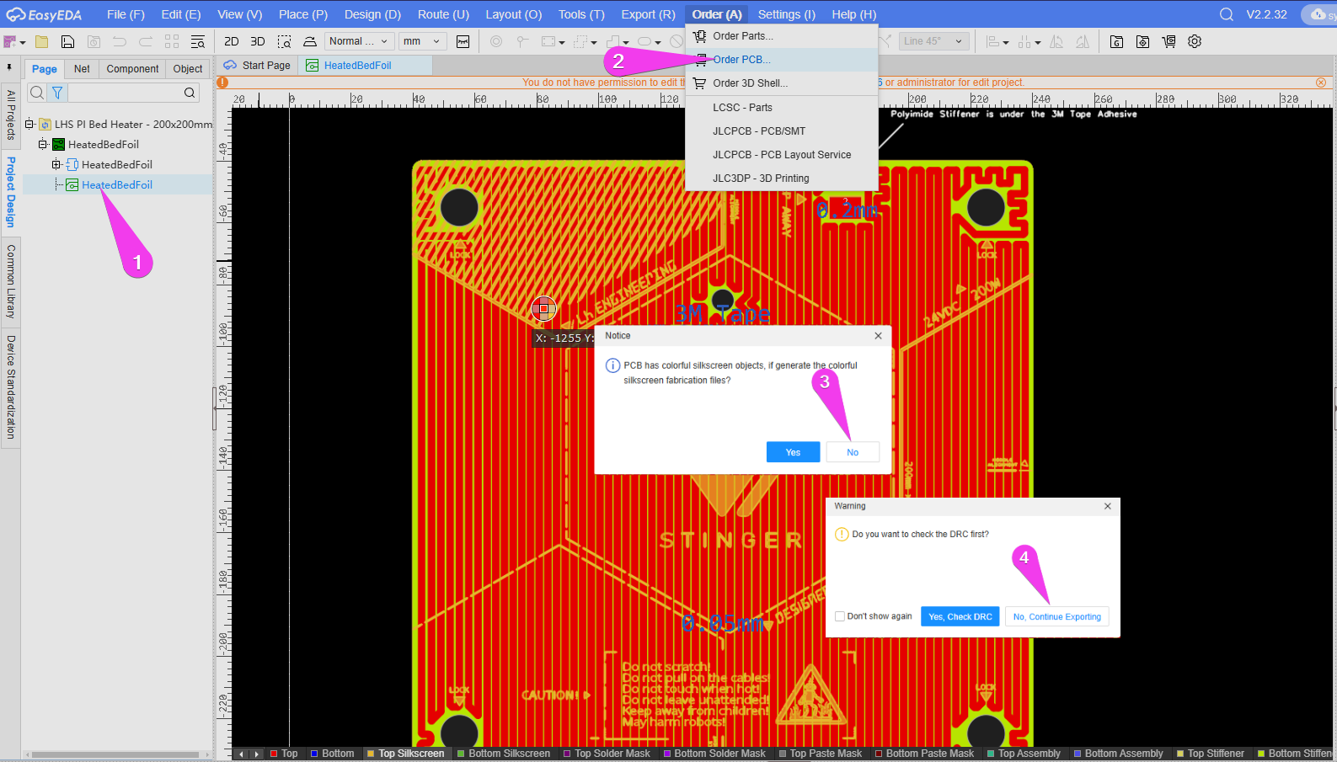
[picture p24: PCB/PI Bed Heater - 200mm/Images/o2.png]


3. Set exactly the following order specifications:
*Note: The minimum order quantity is 5pcs, and the price is for the total order*  
*Share the rest with your friends :wink:*

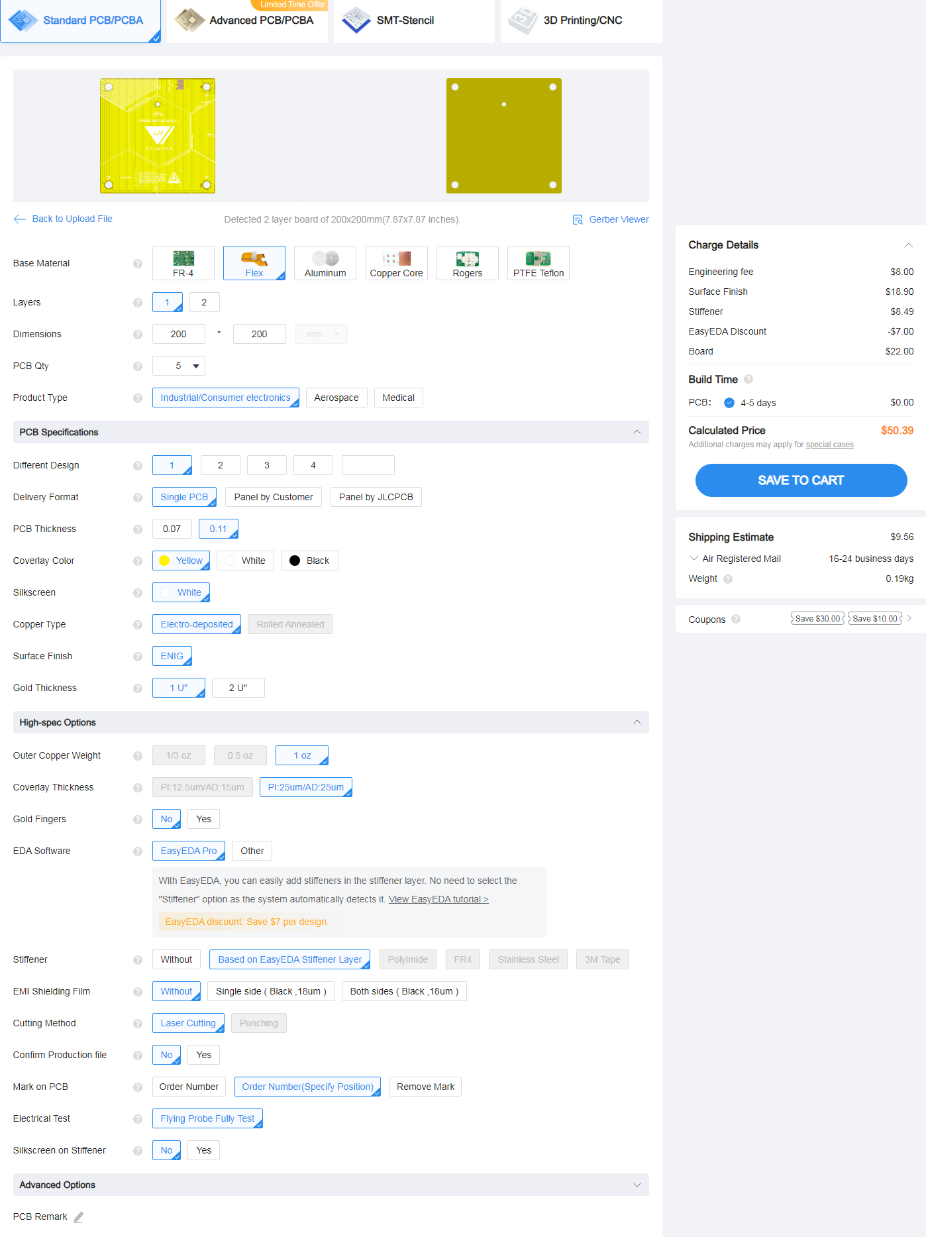
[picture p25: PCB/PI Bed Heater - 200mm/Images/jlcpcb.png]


<br>

# Media

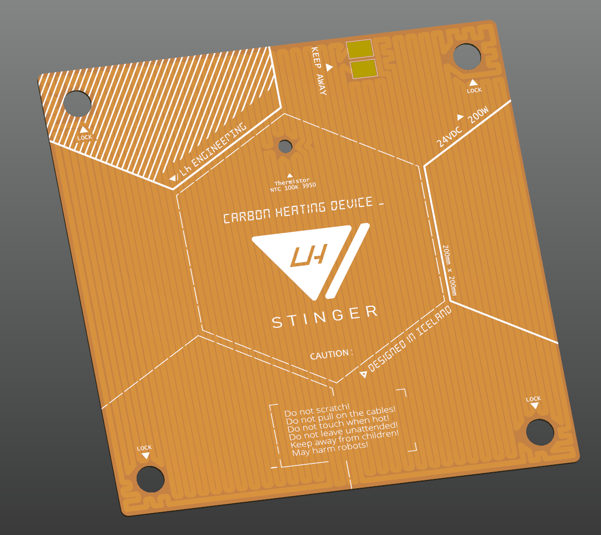
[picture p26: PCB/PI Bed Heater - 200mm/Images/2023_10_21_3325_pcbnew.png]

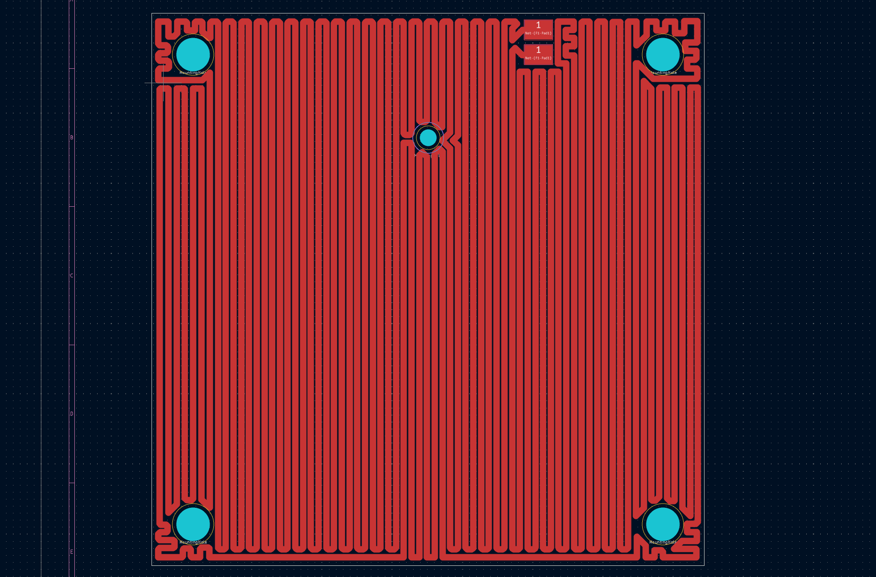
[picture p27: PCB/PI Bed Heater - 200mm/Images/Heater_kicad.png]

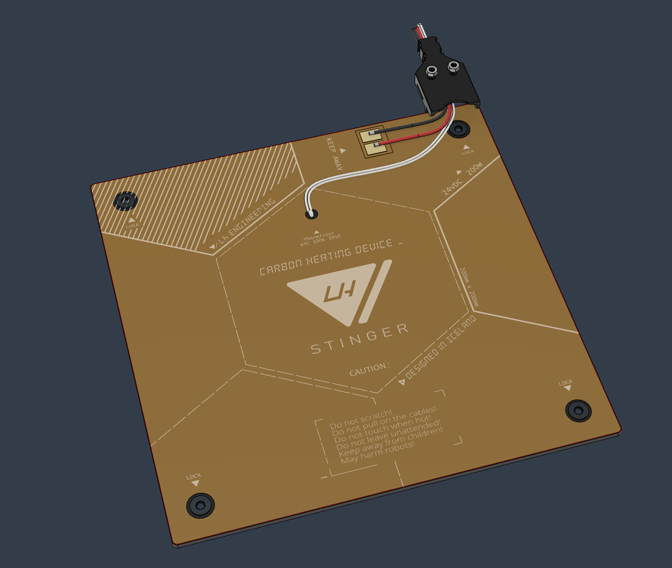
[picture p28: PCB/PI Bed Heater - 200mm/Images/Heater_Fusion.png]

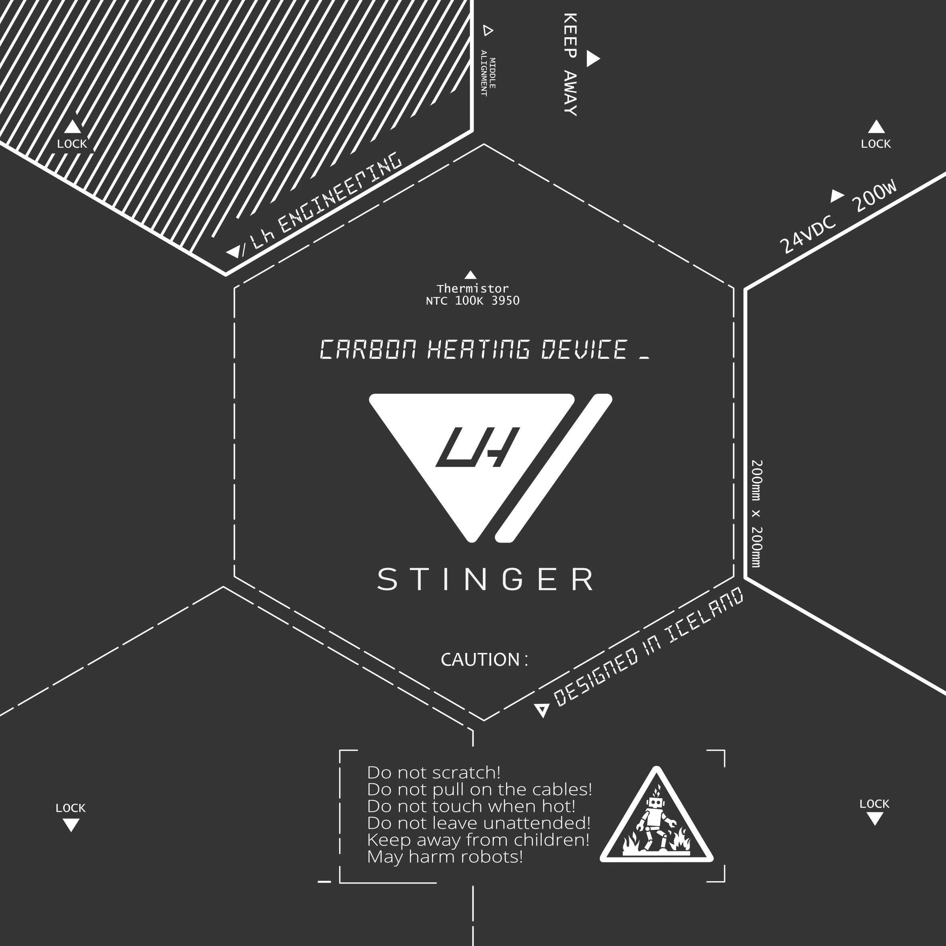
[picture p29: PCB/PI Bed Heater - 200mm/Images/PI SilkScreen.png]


<br>

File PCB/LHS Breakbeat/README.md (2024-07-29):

# LHS Breakbeat

- [LHS Breakbeat](#lhs-breakbeat)
  - [Features](#features)
  - [Specifications](#specifications)
  - [BOM](#bom)
  - [Notes](#notes)
- [Wiring Harness](#wiring-harness)
- [Guide](#guide)
- [Acknowledgments](#acknowledgments)

<br>

**Disclaimer**

>*This is a DIY (Do-It-Yourself) experimental project. This PCB is provided "as is" without any guarantees or warranty, and is not certified for any commercial or critical applications. Use it at your own risk. 
The creator assumes no liability for damages or injuries resulting from its use, including but not limited to fire, electric shock, personal injury or property damage.*
>*By using this PCB, you agree to the terms of this disclaimer.*

<br>

**NOTE: this design is currently in testing**  

<br>

**LHS Breakbeat** is a breakout board built for the LH Stinger, meant to provide an easy interface between the external electronics box and the printer electronics.

This board is meant to be mounted on the printer, and make most of the wiring setup plug and play.

LHS Breakbeat PCB Front

## Features
* Support for 7 stepper motors
* 3 Thermistors
* 3 Fans with individual power requirements
  * 4-pin fan support
* 4 Endstops
* RGB lighting
* Optional probe header
* Filament Sensor (Tach and F Sens pins are shared)
* Fused bed and hotend power lines 
* Support for separate thermistor analog ground
* CAN bus alternative wiring
* Thermistor test points
* Tachometer diode protection

<br>

LHS Breakbeat PCB Front

## Specifications

Note: these guideline limits are on top of your mainboard specifications, along with the wires and connectors used for the wire harness.

Circuit | Limit
--|--
Hotend Heater | 24V, 115W, 4.8 A 
Bed Heater | 24V, 220W, 9.2 A
Fans | 24V, 2 A 
RGB/5V | 2A
Steppers | 2.7 A

## BOM
Please see the [Interactive BOM](https://htmlpreview.github.io/?https://github.com/lhndo/LH-Stinger/blob/main/PCB/LHS%20Breakbeat/BOM/ibom.html)

## Notes

* The BOM included links to paired connectors and crimps
* The Molex MiniFit Paired Power Connector (03-04-4052) requires 16AWG 13A crimps (45750-3112)

<br>

# Wiring Harness

LHS Breakbeat PCB Front

<br>

# Guide

https://github.com/lhndo/LH-Stinger/wiki/Breakout-Box

# Acknowledgments

*Thanks to [@roerich_64](https://github.com/walterwissmann) and the LHS community for the help and guidance with this project!*

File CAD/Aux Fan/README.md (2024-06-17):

❗ Make a folder first in Fusion360 in which to upload and open the Aux Fan.f3z or any other .f3z file.  
This is a archive format that contains all the linked assemblies and component instances. Otherwise the upload will "explode" all the individual files into your main working folder.  

[**Aux Fan** - Online CAD Viewer  ](http://tiny.cc/lhs-aux)   

[**Aux Fan - Assembly and Configuration Guide**](https://github.com/lhndo/LH-Stinger/wiki/Aux-Fan)

<br>

Preview    

Preview

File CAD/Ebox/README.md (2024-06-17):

❗ Make a folder first in Fusion360 in which to upload and open the Ebox.f3z or any other .f3z file.  
This is a archive format that contains all the linked assemblies and component instances. Otherwise the upload will "explode" all the individual files into your main working folder.  

[**Ebox** - Online CAD Viewer  ](http://tiny.cc/lhs-ebox)
[**Breakout Box** - Online CAD Viewer  ](http://tiny.cc/lhs-breakout) 

 <br>

Preview

<br>

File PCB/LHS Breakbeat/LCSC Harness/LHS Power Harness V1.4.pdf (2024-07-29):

UL3135 AWG16 (1000±15mm); SVS1.25-4 *2pcs; 2204.0 *2pcs; Φ9.0*800黑色编织网管; (39000038) UL1332 AWG22; Orange Blue White Black Red; White; Black; Red; Orange Blue; XHP-2 *1PCS

日 | 期
日 | 期
单 | 位
审 | 核
绘 | 图

客户料号

品名规格

客 户

LHS POWER HARNESS V1.3

技术要求：
1.线材不可有刮伤，漏铜丝等不良现象。
2.线材须符合ROHS标准，端子与线材拉力为国际标准。 3.锡口部位需圆润光滑，不可有分叉，断铜丝等不良现象。

MOLEX

Black braid tube

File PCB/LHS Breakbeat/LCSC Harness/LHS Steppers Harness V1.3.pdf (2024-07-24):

插线方向孔位示意图; XHP-4 *4PCS SXH-001T-P0.6 *16PCS; UL1332 AWG24 (1500±15mm); 裁线：1015mm 红、黑、绿、蓝 各*6PCS; Φ9.0*800黑色编织网管; Red-2 Blue-14 Green-1 Black-13; Red-4 Blue-16 Green-3 Black-15; Red-6 Blue-18 Green-5 Black-17; Red-8 Blue-20 Green-7 Black-19; Red-10 Blue-22 Green-9 Black-21; Black braid tube

日 | 期
日 | 期
单 | 位
审 | 核
绘 | 图

客户料号

品名规格

客 户

LHS STEPPERS HARNESS V1.3

技术要求：
1.线材不可有刮伤，漏铜丝等不良现象。
2.线材须符合ROHS标准，端子与线材拉力为国际标准。 3. 锡口部位需圆润光滑，不可有分叉，断铜丝等不良现象。

Red-12
Blue-24
Green-11
Black-23

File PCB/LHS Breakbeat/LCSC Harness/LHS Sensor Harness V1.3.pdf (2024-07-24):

XHP-4 *2PCS XHP-3 *5PCS XHP-2 *6PCS SXH-001T-P0.6*20PCS A2547H-3P *2PCS A2547-TP *2PCS; 插线方向孔位示意图; UL1332 AWG24 (1000±15mm); 裁线：1515mm 黄 *10PCS 灰 *5PCS 红 *5PCS 绿、蓝 各*1PCS; Φ9.0*800黑色编织网管; Black braid tube; Gray 6 Red 1; Yellow-20; 9-Yellow; Gray 13 Red-3 Gray-4 Red-7 Gray-19 Yellow-11 Yellow-10; Yellow-12 Red-21 22-Yellow; 2-Yellow; 5-Yellow; 5-Yellow Red-18 Blue-17 Green-16 Gray-15; Yellow-14

日 | 期
日 | 期
单 | 位
审 | 核
绘 | 图

客户料号

品名规格

LHS SENSORS HARNESS V1.3

客 户

技术要求：
1.线材不可有刮伤，漏铜丝等不良现象。
2.线材须符合ROHS标准，端子与线材拉力为国际标准。 3.锡口部位需圆润光滑，不可有分叉，断铜丝等不良现象。

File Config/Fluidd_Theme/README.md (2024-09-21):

  [:arrow_double_down: Download Folder](https://download-directory.github.io/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)

# LH Stinger Fluidd Theme


   
## Installation

1. Place these files inside a `.fluidd-theme` folder located in your main `/config/` folder.  
2. Open **Settings**, nagivate to '**Fluidd settings in Moonraker database**'  
3. Choose `Restore`and load the `backup-fluidd.json` file provided here.
4. Refresh the website

<br>

### Credits

 *Built on the custom.css from [Fluid theme simple](https://github.com/bumbeng/Fluidd_theme_simple) by [bumbeng ](https://github.com/bumbeng)*

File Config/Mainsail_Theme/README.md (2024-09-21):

[:arrow_double_down: Download Folder](https://download-directory.github.io/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)

# LH Stinger Mainsail Theme


   
## Installation

1. Place these files inside a "**.theme**" folder located in your main **/config/** folder.  
2. Open Settings, click restore and choose the **backup-mainsail.json** provided here.



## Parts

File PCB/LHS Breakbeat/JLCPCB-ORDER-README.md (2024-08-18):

## JLCPCB Ordering

Download **LHS Breakbeat JLCPCB.zip**

1. Upload the zip from the the **production_files** folder
2. Use the order settings below. Keep an eye on the pricing when selecting options
3. Check Assembly and proceed with the steps and Confirm.
4. Upload the .csv files
5. Ignore Fiducials
6. Confirm the parts in the stock or choose alternatives if not available.
7. Move the components out of position roughly to their places. (Ignore the ones missing models such as the XT60)

## Order Details

<br>

Base Material: FR-4  
Layers: 2  
Dimension: 114 mm* 61.4 mm 114mm* 61.4mm  

<br>

PCB Qty: 5  
Product Type: Industrial/Consumer electronics  

<br>

Different Design: 1  
Delivery Format: Single PCB  
PCB Thickness: 1.6  
Impedance Control: no  
PCB Color: Blue  (Note: Prices change a lot between options. Other colors might be cheaper)
Silkscreen: White  
Material Type: FR4-Standard TG 135-140  

<br>

Via Covering: Tented  
Surface Finish: HASL/ENIG (Note: Change between this option along with the board colors to find a lower price)
Deburring/Edge rounding: No  
Outer Copper Weight: 2 oz  
Flying Probe Test: Fully Test  
Castellated Holes: no  
Edge Plating: No  
Remove Order Number: Specify a location  
4-Wire Kelvin Test: No  
Paper between PCBs: No  
Appearance Quality: IPC Class 2 Standard  
Confirm Production file: Yes  
Silkscreen Technology: Ink-jet/Screen Printing Silkscreen  
Board Outline Tolerance: ±0.2mm(Regular)  

<br>

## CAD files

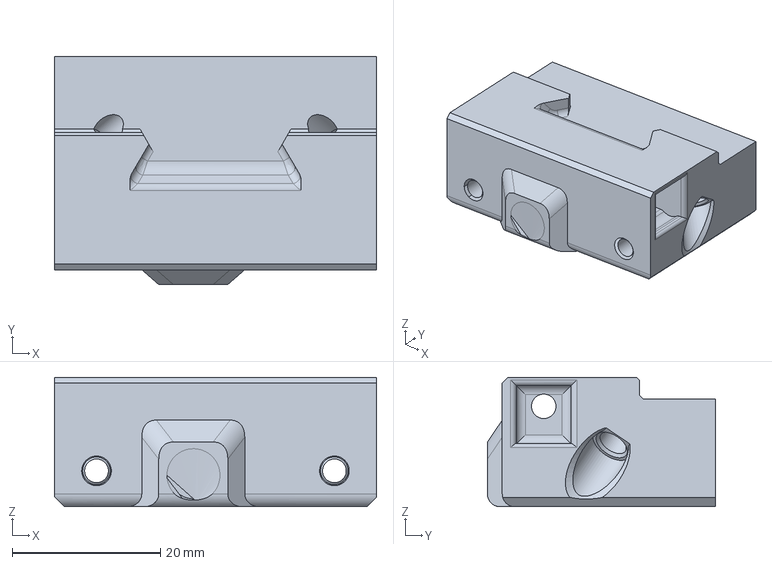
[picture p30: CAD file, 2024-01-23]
User_Mods/Toolhead/X Tensioner w Kusuba mount - @Killajoedotcom/KUSBA X Tensioner Main Body.step
43.5 x 30.8 x 17.5 mm

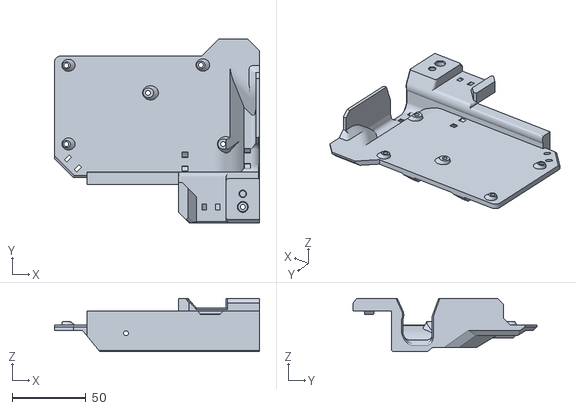
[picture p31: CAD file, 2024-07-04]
STL/Printer/Breakout Box/Breakout Main Body.stl
138.6 x 124.4 x 36.0

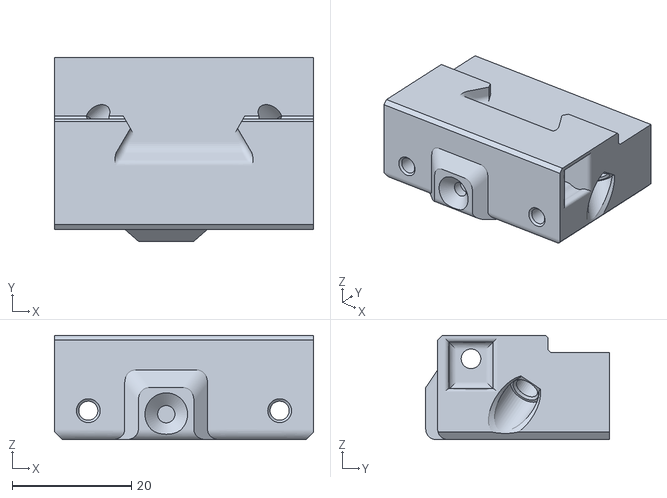
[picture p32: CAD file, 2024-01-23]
User_Mods/Toolhead/X Tensioner w Kusuba mount - @Killajoedotcom/X Tensioner Main Body.stl
43.5 x 30.8 x 17.5

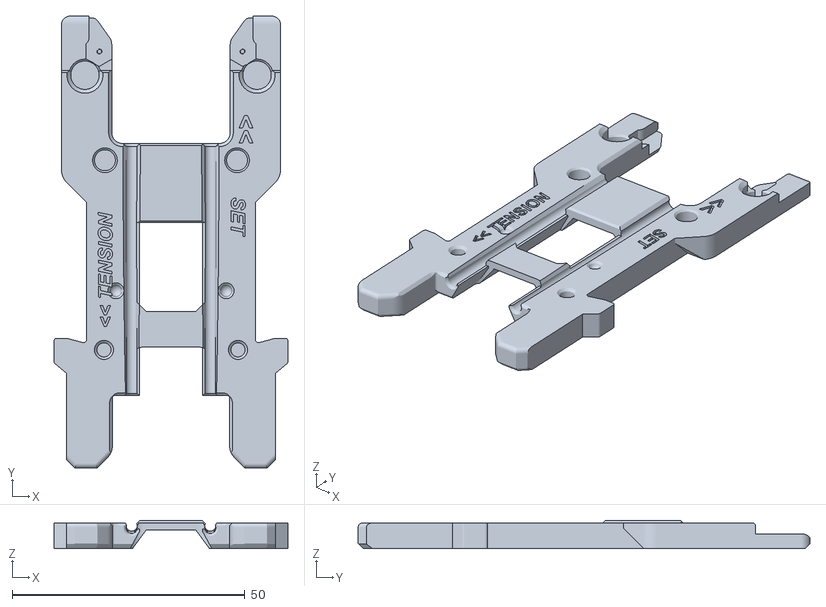
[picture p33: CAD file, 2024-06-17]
STL/Other/Y Belt Tool Main.stl
50.3 x 97.0 x 6.09

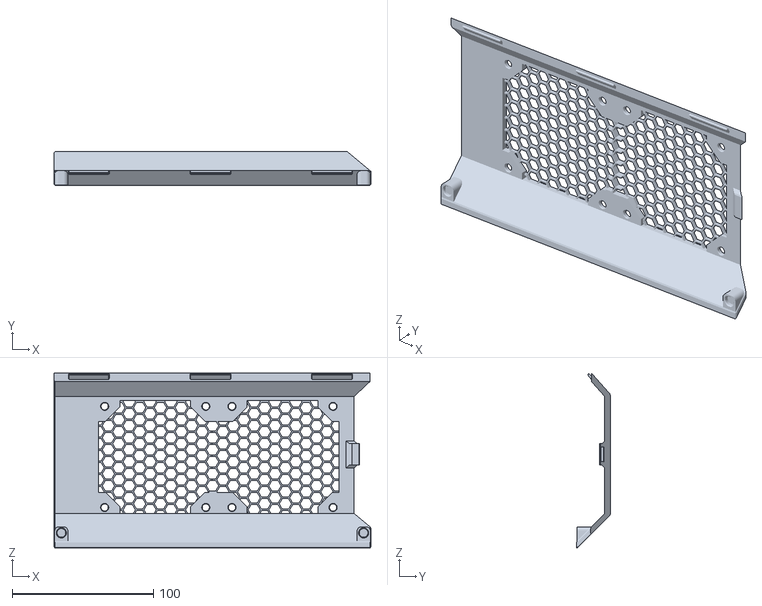
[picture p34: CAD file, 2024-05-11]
User_Mods/Ebox/80mm Fan Door - @Wight554/Door Main M5.stl
224.2 x 23.8 x 123.7

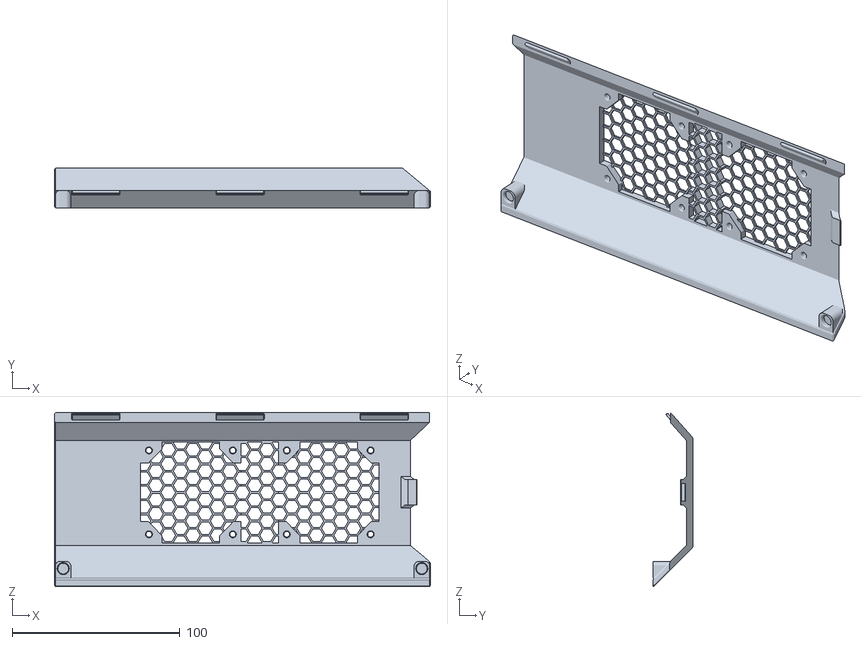
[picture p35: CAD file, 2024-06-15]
STL/Ebox/Door Main.stl
224.2 x 23.8 x 103.7

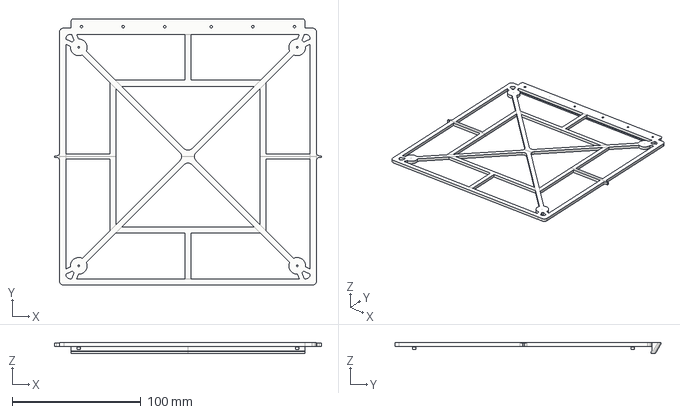
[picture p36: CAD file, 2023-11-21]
CAD/Other/Bed Heater Alignment Jig.step
207.8 x 207.4 x 8.30 mm

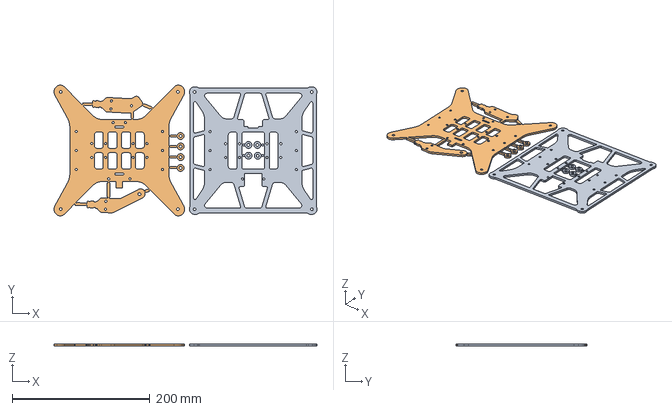
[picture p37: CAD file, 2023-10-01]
DXF/CF_Carriage_Plates.step
381.4 x 189.6 x 3.00 mm

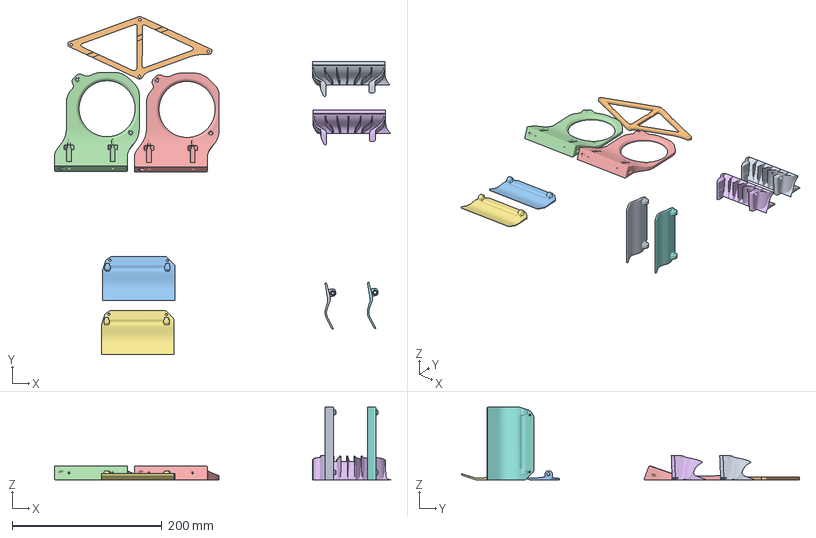
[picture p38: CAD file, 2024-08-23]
STL/Aux Fan Parts.3mf
449.0 x 451.5 x 97.1 mm
AC Fins x2.stl x 2
Botton Bracket.stl
Flap x2.stl x 2
Top x2.stl x 2
Flap UHF x2.stl x 2

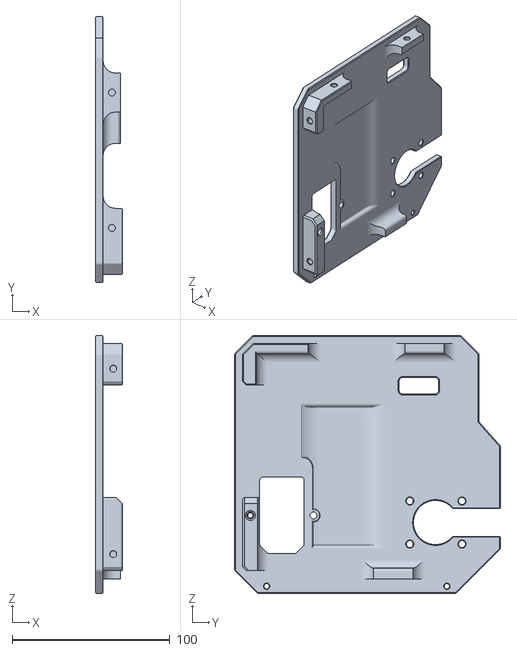
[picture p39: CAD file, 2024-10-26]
STL/Ebox/Panel Right.stl
17.4 x 168.8 x 163.9

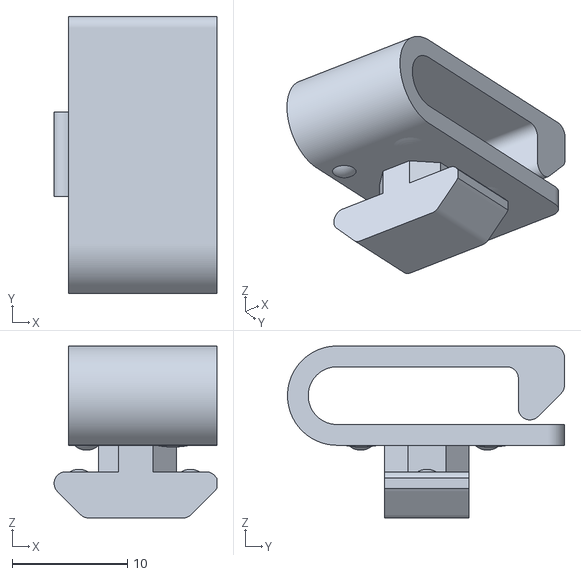
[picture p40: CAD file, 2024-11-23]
STL/Other/3030 Cable Clamp 90D x6.stl
14.1 x 24.0 x 14.9

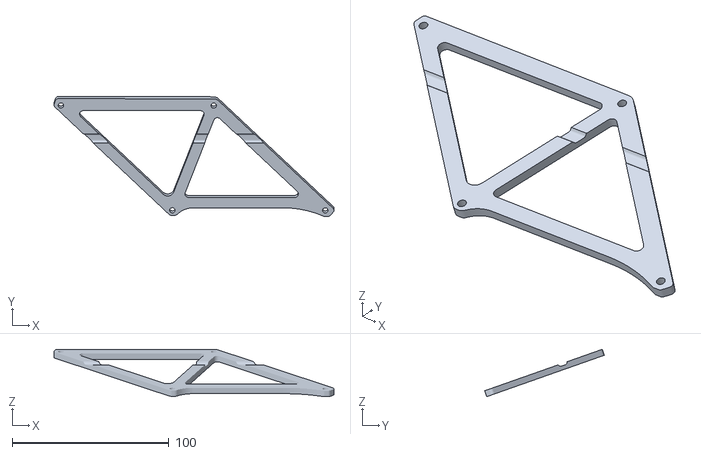
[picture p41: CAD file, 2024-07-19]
STL/Printer/Aux Fan/Bottom Bracket.stl
178.7 x 76.4 x 30.2

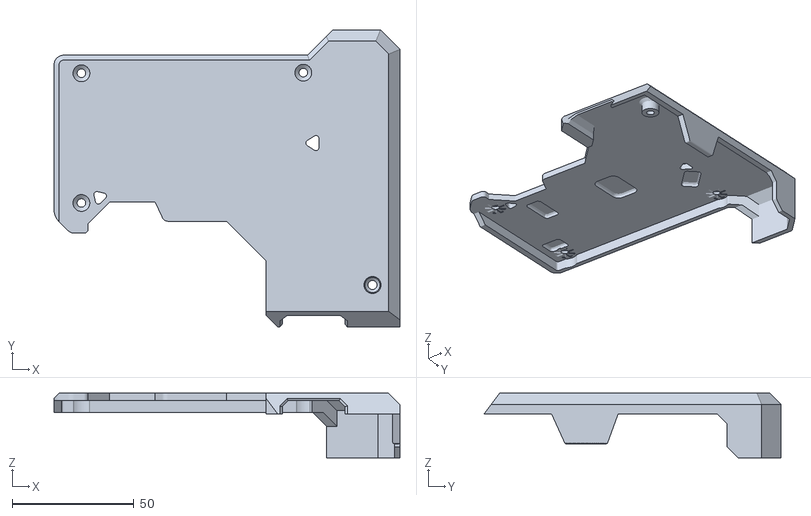
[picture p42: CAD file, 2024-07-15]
STL/Printer/Breakout Box/Breakout Top Plate.stl
141.9 x 122.0 x 26.5

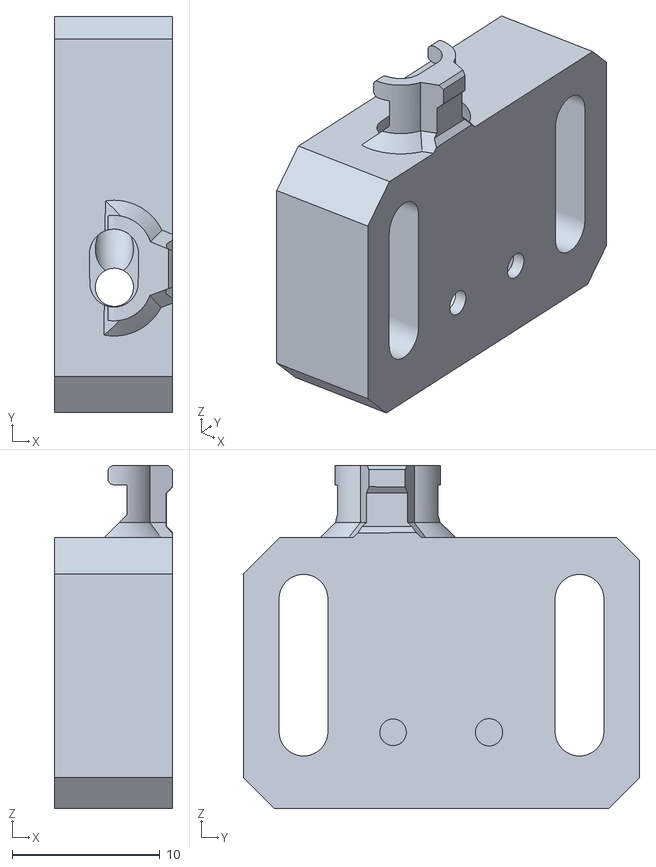
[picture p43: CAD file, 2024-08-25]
STL/Printer/Endstops/Z Endstop.stl
8.00 x 26.8 x 23.2

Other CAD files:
User_Mods/Ebox/80mm Fan Door - @Wight554/Door Main.stl
STL/Printer/Toolhead/Toolhead Tensioner.stl
STL/Printer/X/X Bearing Insert.stl
STL/Printer/Y/AC Y Belt Tensioner - Tolerance ++.stl
DXF/CF_Bed_200mm2_x3mm.dxf
DXF/CF_Bed_200mm2_x3mm.step
DXF/CF_Carriage_Plates.dxf
STL/Breakout Box Parts.3mf
STL/Ebox Parts.3mf
STL/Ebox/AC Cable Guide Large.stl
STL/Ebox/AC Cable Guide Low Large.stl
STL/Ebox/AC Cable Guide Low Small.stl
STL/Ebox/AC Cable Guide Small.stl
STL/Ebox/AC Cable Guide Top Large x2.stl
STL/Ebox/AC Cable Guide Top Small x2.stl
STL/Ebox/AC Cable Port Trim.stl
STL/Ebox/AC Wago Mount x3.stl
STL/Ebox/Cable Port A.stl
STL/Ebox/Cable Port B.stl
STL/Ebox/Door Side Cap.stl
STL/Ebox/Door Top.stl
STL/Ebox/Foot x4.stl
STL/Ebox/Hinge A x2.stl
STL/Ebox/Hinge B x2.stl
STL/Ebox/Magnet Base Left.stl
STL/Ebox/Magnet Base Right.stl
STL/Ebox/Mount Octopus Pro.stl
STL/Ebox/Mount Pi (Rasp, BTT).stl
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

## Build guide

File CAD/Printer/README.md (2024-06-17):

❗ Make a folder first in Fusion360 in which to upload and open the LH Stinger.f3z file.  
This is a archive format that contains all the linked assemblies and component instances. Otherwise the upload will "explode" all the individual files into your main working folder.  

[**Printer** - Online CAD Viewer  ](http://tiny.cc/lhs-printer)  
[**Toolhead** - Online CAD Viewer  ](http://tiny.cc/lhs-toolhead)  

>Note: The CAD file contains a set of hidden components and instructions to aid the assembly process.

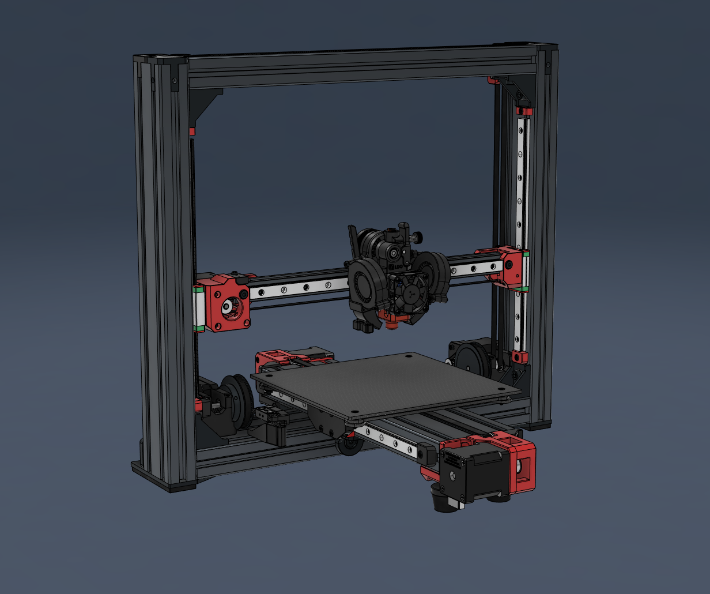
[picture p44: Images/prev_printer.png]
Preview


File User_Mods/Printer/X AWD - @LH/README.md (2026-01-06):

## X AWD

**Contents:**

  - [Parts Required](#parts-required)
  - [Printed Parts](#printed-parts)
  - [Assembly](#assembly)
  - [Belt Tension](#belt-tension)
  - [Stepper Sync](#stepper-sync)
  - [Notes](#notes)

<br>

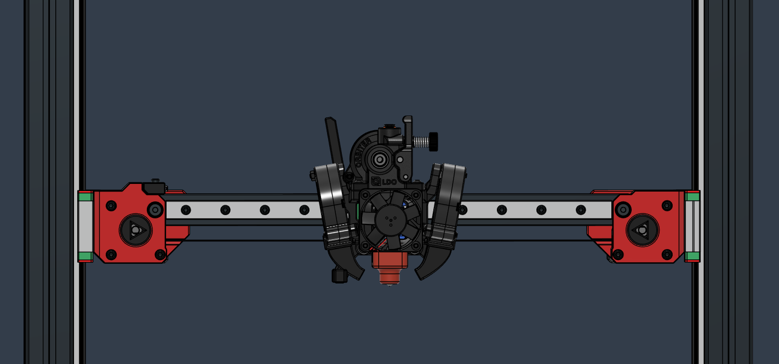
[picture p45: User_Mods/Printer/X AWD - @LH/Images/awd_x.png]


<br>

### Parts Required

* :exclamation: Stepper motors, stepper drivers and pulleys have to be identical to their left counterparts.
* The pulleys on the LH Stinger were sourced specifically to match the required dimensions, the correct belt profile and the desired quality.  
(Gates or Runice pulleys are highly recommended)

<br>  

*Existing parts from the single X configuration were not excluded from tables below.*  

<br>

**Driver**

| Type | Item  |  Quantity |
|---|---|---|
Driver | TMC 2240| 1
Wiring | Stepper Motor Cable | 1

<br>

**AWD X Gantry**

*Note:*  
* *Most use the existing X extrusion/rail and custom cut it to the dimensions listed below.*  

| Type | Item  |  Quantity |
|---|---|---|
Extrusion | 2020 - 304 mm| 1
Linear Rail | MGN12H - 282 mm | 1

<br>

**AWD X Right Mount**

| Type | Item  |  Quantity |
|---|---|---|
Motor | LDO Nema_17_42STH48-2504AC| 1
Pulley |2GT-20T - For 6mm Belt| 1
Bearing | 625 2RS | 1
Heat Insert | M3 Short 5x4 | 1
T-Nut - Square | 2020 - M5 | 2
Hex Nut | M3 | 1
Shim | 7 x 5 x 0.5mm | 2
Shim | 10 x 5 x 1mm | 1
Screw Socket Head | M3 14mm | 2
Screw Socket Head | M3 12mm | 1
Screw Button Head | M3 10mm | 3
Screw Socket Head | M3 22mm | 1
Screw Socket Head | M3 35mm | 2
Screw Button Head | M3 12mm | 1
Screw Socket Head | M5 10mm Low Head | 1
Screw Socket Head | M5 12mm | 1

<br>

**AWD Z Right Mount**

*Note:*  
* *This includes the complete list of parts for a new Z drive assembly*  
* *Realistically you would probably only need an extra bearing, a longer shaft (can be longer than stated size) and a couple of fasteners.*  

| Type | Item  |  Quantity |
|---|---|---|
 Motor | Nema 17 LDO-42STH40-1684AC | 1
Pulley |  2GT-20T 6mm | 2
Pulley | 80T 6mm | 1
Bearing | 625 2RS | 3
Shim | 10 x 5 x 1mm | 4
Shaft | D Shape -  72mm x 5mm | 1
Belt | 2mgt 6mm 188mm Closed Loop | 1
Heat Insert | M3 Long 4.6x5.7 | 6
T-Nut Drop In | 3030 - M3 | 3
Washer | M4 9 x 0.5mm | 1
Washer | M3 7x0.5mm | 6
Screw Socket Head | M3 12mm | 4
Screw Socket Head | M3 22mm | 2
Screw Socket Head | M3 30mm | 6

<br>

### Printed Parts

An Orca Slicer **AWD X.3mf** project file is available in the files above. 

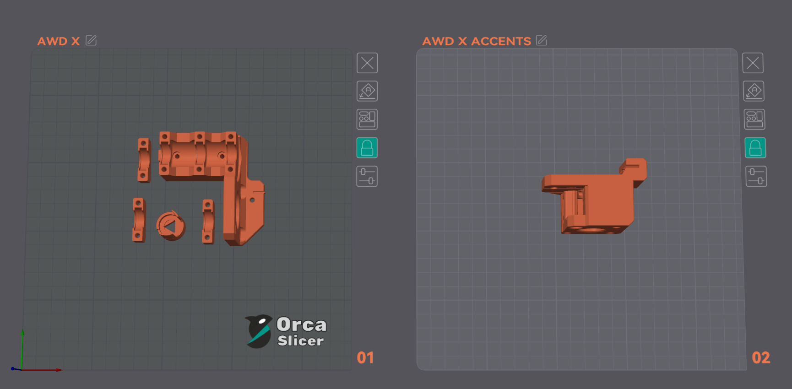
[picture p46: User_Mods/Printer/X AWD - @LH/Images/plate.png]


<br>

### Assembly

Please follow the instructions of the left counterparts in the main [Assembly Guide](https://github.com/lhndo/LH-Stinger/wiki/Assembly-Guide) 

* [X Mount Assembly](https://github.com/lhndo/LH-Stinger/wiki/Assembly-Guide#x-mounts)
* [Z Mount Assembly](https://github.com/lhndo/LH-Stinger/wiki/Assembly-Guide#z-mount-assembly)

**Note:**
* Markings are embedded on each part for identification. 

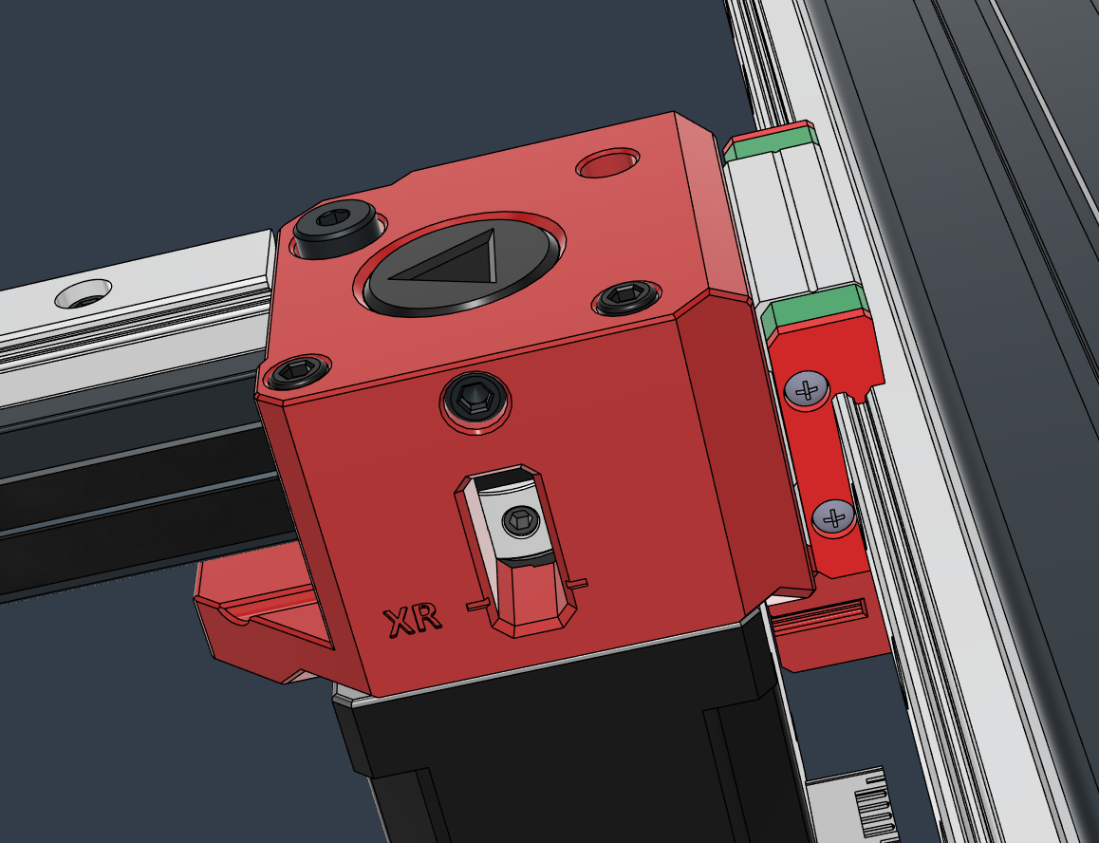
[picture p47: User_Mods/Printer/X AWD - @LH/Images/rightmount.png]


<br>

* The X motor pulley requires a 1.7mm offset from the stepper face, with the middle of the belt sitting at a 13mm offset  
* :exclamation: The right side pulley is mounted with the grub screws on the round part of the shaft on the right stepper motor, otherwise the stepper cannot be synced together
    * Make a mark with a Sharpie at the end of the motor shaft to indicate the flat D slot location

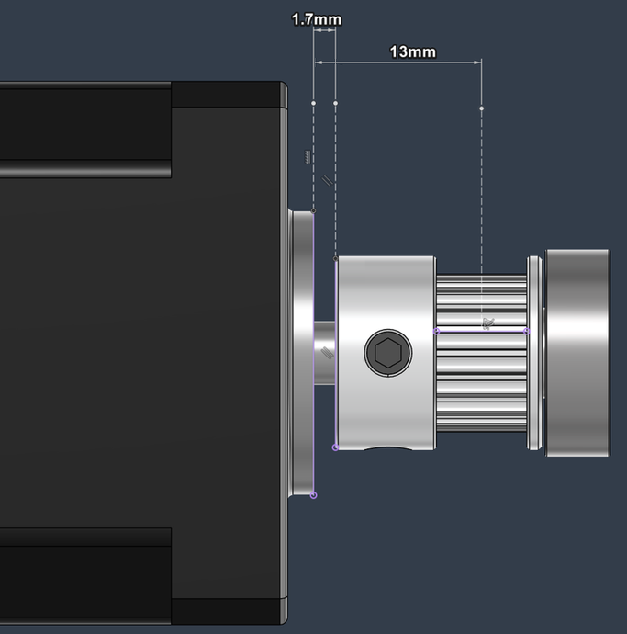
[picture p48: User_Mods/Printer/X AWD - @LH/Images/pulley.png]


<br>

### Belt Tension

* Move the carriage all the way to the left
* Loosen both grub screws on the right pulley
* Tension the belt to 116hz (~6.5 lbf over a **256mm** measured belt span)
* Perform the X Stepper Sync procedure and tighten the grub screws at the end

For more information please consult the [Tuning - Belt Tension Guide](https://github.com/lhndo/LH-Stinger/wiki/Tuning#belt-tension)

<br> 

### Stepper Sync

* The X stepper sync procedure is performed on the right side of the mount
  * Perform Z-Tilt procedure first, then raise the gantry to the top of the printer
  * Loosen the grub screws though the bottom access window of the mount
  * Perform the sync procedure as described in the [Tuning Guide - Syncing Stepper Motors](https://github.com/lhndo/LH-Stinger/wiki/Tuning#syncing-stepper-motors)

<br>

### Notes

* 100% nozzle coverage is maintained on the 235mm bed, with some probe dead zone on the right edge

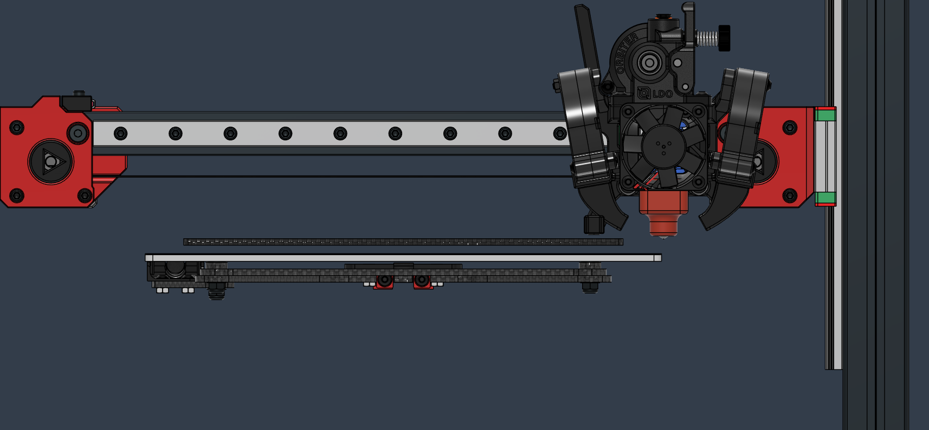
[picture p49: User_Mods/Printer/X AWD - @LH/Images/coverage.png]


<br>

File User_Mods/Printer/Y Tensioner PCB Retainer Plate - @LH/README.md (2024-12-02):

# Y Tensioner PCB Retailer Plate

Replaces the printed plate holding the Y tensioner block and provides better stiffness and temperature resistance.

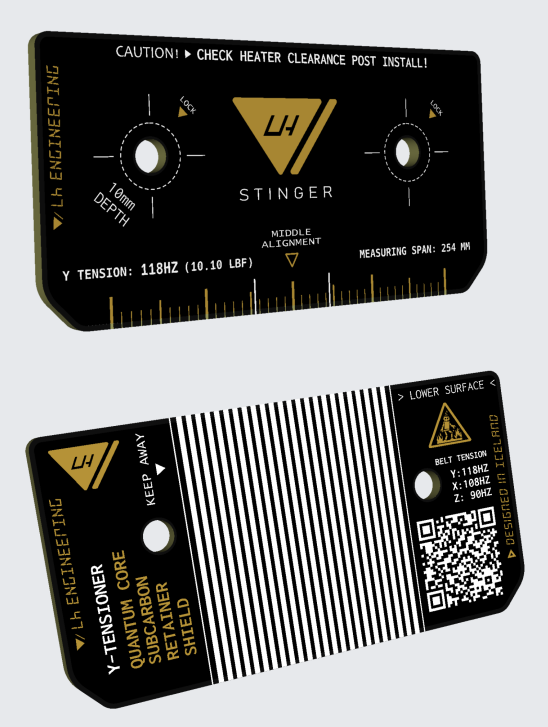
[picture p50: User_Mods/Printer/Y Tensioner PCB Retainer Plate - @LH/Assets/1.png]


## Installation

* Mount with two M3 10mm Button Head Screws
* Check for clearance between the top of the screws and the heater 
<br>

## Ordering

**PCBWay**

 [Y Tensioner PCB Retailer Plate](https://www.pcbway.com/project/shareproject/LH_Stinger_Y_Tensioner_PCB_Retainer_Plate_a8267ae3.html)

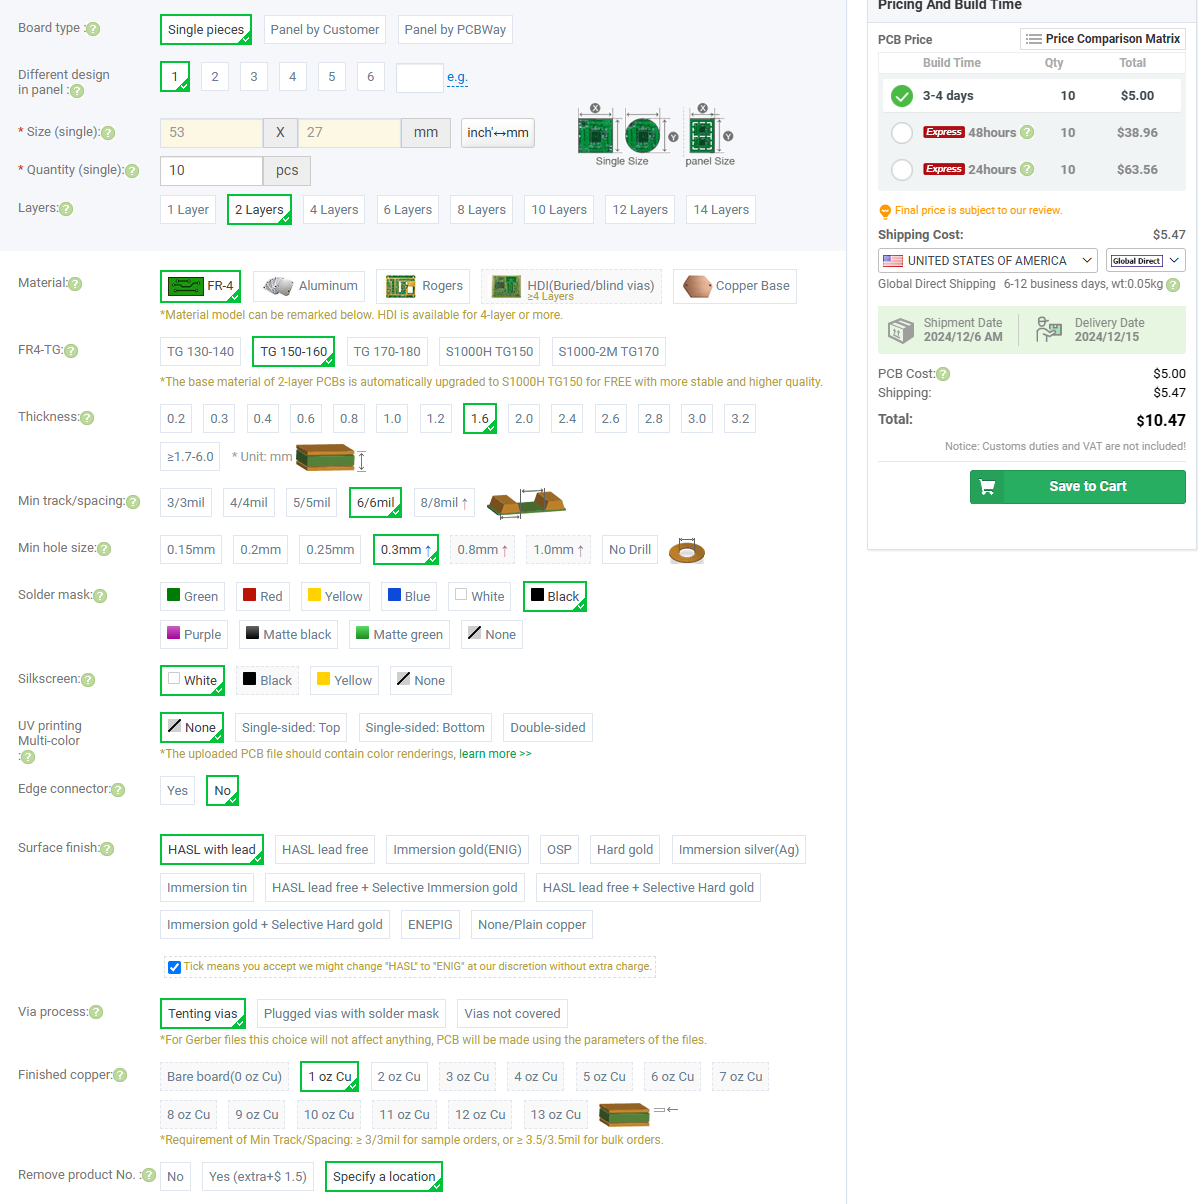
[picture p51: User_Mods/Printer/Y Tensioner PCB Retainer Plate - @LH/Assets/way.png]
 

<br>

**JLCPCB**

1. Upload Gerber.zip to [jlcpcb.com](https://jlcpcb.com)
2. Choose your color
3. Set "Mark on PCB: Remove Mark"

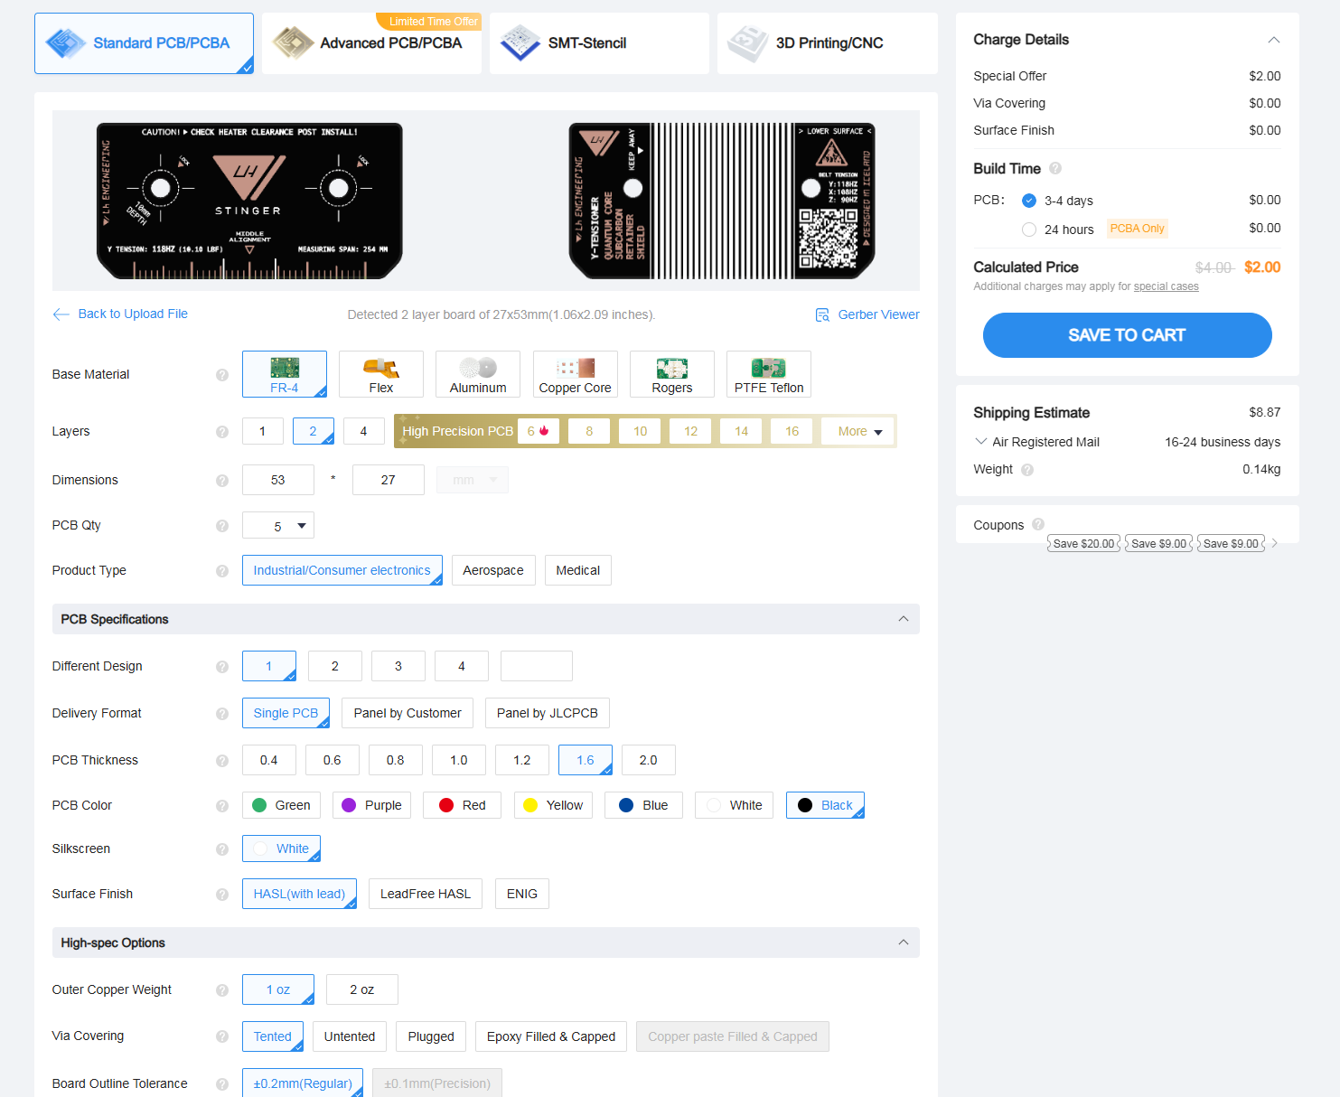
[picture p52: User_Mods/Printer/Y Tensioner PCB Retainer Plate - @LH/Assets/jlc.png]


<br>

## Images

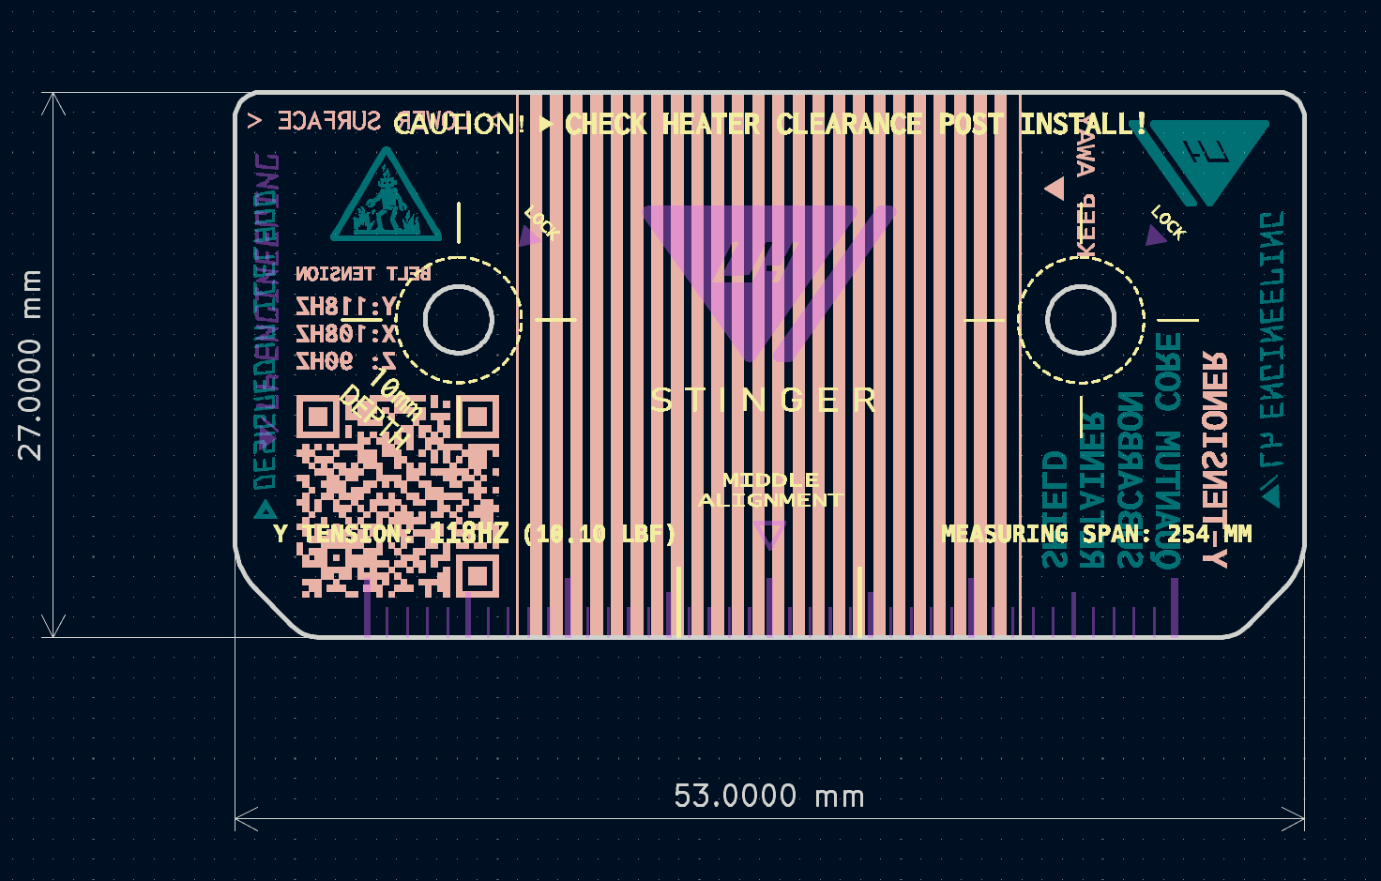
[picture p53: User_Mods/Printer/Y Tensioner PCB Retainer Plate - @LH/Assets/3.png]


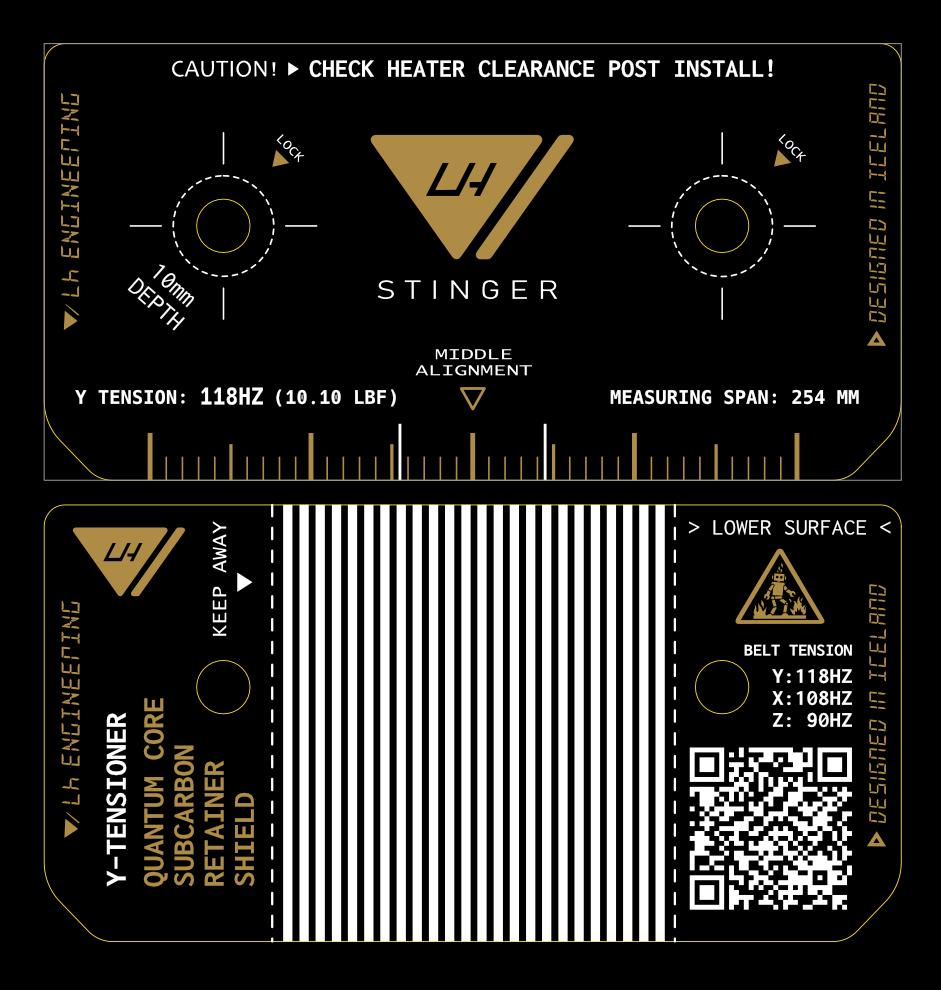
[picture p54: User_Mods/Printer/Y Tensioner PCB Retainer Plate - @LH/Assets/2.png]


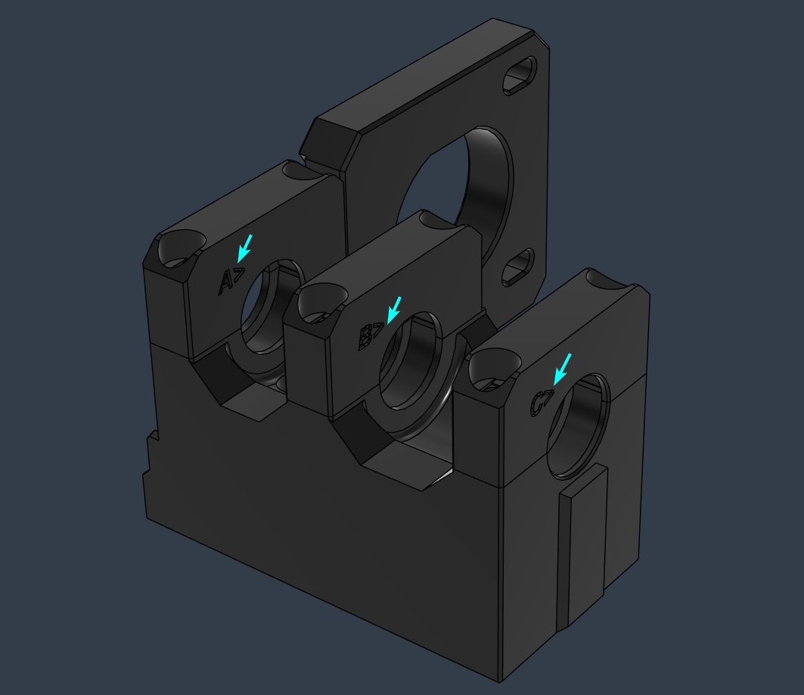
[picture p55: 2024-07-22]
User_Mods/Printer/X AWD - @LH/Images/abc.png

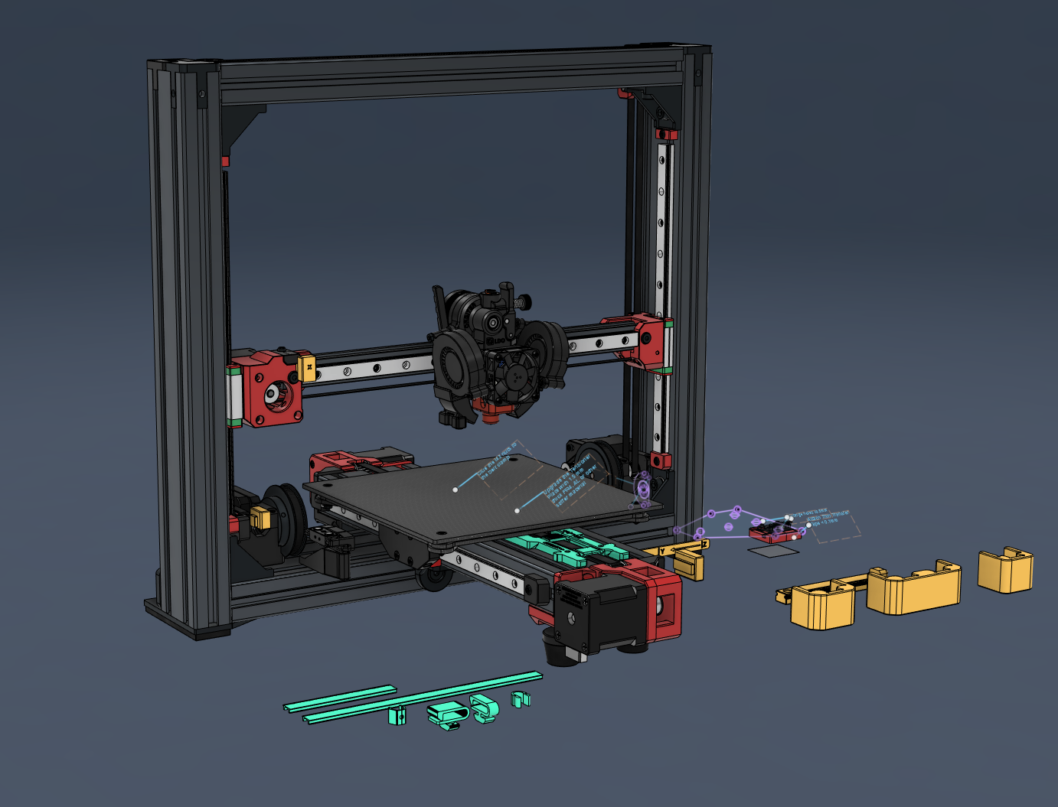
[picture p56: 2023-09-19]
Images/prev_printer2.png

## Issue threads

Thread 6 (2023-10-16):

Printer cad file is not opening

Shamoon78, 2023-10-16:
The printer cad file is broken canot be extracted

lhndo, 2023-10-16:
Hi,
Is it the fusion or the step file?
Does it fail when extracting or when trying to open it in a CAD program? If so, in what program?

Shamoon78, 2023-10-17:
It is the step file and give me error when extracting the file

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

walterwissmann, 2023-10-17:
Hey @Shamoon78

I have no problem to extract the 'LH Stinger.step.zip' on Linux Mint.
See:
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

BR
Walter

lhndo, 2023-10-17:
> It is the step file and give me error when extracting the file

Can you try downloading the archive again with another browser? Maybe the download was corrupted.
What program are you using to extract it, so I could try to reproduce the issue.

Shamoon78, 2023-10-17:
I am using windows 11 and using the built in software for windows 11 ,win
10 used to need a program to extract certain files but win 11 can extract
all kinds of files. This is the first issue for me but happy to give 7 zip
a try and see how it goes .

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

lhndo, 2023-10-17:
It should be fixed now

walterwissmann, 2023-10-17:
On Linux Mint / FreeCAD it runs ;-)

Shamoon78, 2023-10-17:
Thank you

On Wed, 18 Oct 2023 at 04:44, walterwissmann ***@***.***>
wrote:

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

Closed 2023-10-17.

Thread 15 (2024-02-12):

Breakout PCB Part Sourcing

lhndo, 2024-02-12:

iNinja9k, 2024-12-14:
bro how can i get a board?

lhndo, 2024-12-14:
> bro how can i get a board?

Fysetc sells a kit pcb kit that includes the harnesses on their website. Ping me if you get it because there are some pins that need to be flipped depending on your board.

iNinja9k, 2024-12-14:
thanks for the info bro, appreciate it.
PDank Douglas Korytkowski

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

iNinja9k, 2024-12-15:
OMG 800 dollar kit geeze I don't know if the price to performance is worth
it even to build this now do you think I could source the parts cheaper or
use substitutes for some parts will a normal like big tree board work for
the breakout fans and such. I mean any raspberry pi will work for klipper.
PDank Douglas Korytkowski

On Sat, Dec 14, 2024, 6:59 PM Douglas Korytkowski Jr <
***@***.***> wrote:

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

lhndo, 2024-12-15:
I meant the breakout board which is 29.9 or something. There's a link for it in the Stinger BOM as well.

Closed 2024-03-20.

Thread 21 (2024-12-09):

NOT AN ISSUE - an idea / suggestion

billbrach, 2024-12-09:
Could this PCB design not be made directly on 3-4MM G10/FR4, and use that as the actual surface to print on ??

I am tired with every 3D printer that I've bought, the aluminum bed warping.  Almost always, they end up low in the middle.  If this PCB foil pattern could be directly etched on a correctly sized/thickness of G10, you could eliminate having to glue/stick this to the actual print bed.

Thanks for reading !!

lhndo, 2024-12-09:
Hi Bill, That is what the PRUSA beds are made of and you can check those out here: https://github.com/prusa3d/Heatbed_MK52_magnetic/ . There are many aftermarket sources where you can buy those directly, in mk3/4 size or mini

 I have looked into FR4, but in the LH Stinger case it's way too bendy for the indented use. The CFRP build plate forms a rigid assembly with the carriage providing a very sturdy platform. To some degree both the FR4 and the CFRP can bend and the final flatness is dependent on how the entire assembly is tuned against the rail carts. Depending on that it can vary between 1mm to 0.08mm ranges. The surface is very stable when heated.

billbrach, 2024-12-13:
Thanks, I'm looking for bigger beds, in the Ender 3 size, 235 x 235.  It seems to me, as the folks at JLCPCB, could print this directly on either aluminum, or thicker G10/FR4, that that might be an option.

BTW, how did you create the back and forth pattern of the traces on the PCB film that you did ?? Is that all done by hand, or is there a way to lay those down.  Cover the entire surface in copper, then remove areas to make the traces ??  I'm no novice to EasyEDA, having done 25 different PCB designs now, over the last 3 years, and working on more !!

lhndo, 2024-12-13:
You can epoxy, tape or glue the FR4 heater on whatever surface you want, so you don't have to get something done though an expensive process. For example, I believe that Prusa sacrifices one of the bed PCBs in which they route slots for magnets, and then they glue it together with the actual working heater PCB. This way they have a sandwich of 2 FR4 plates with a larger end thickness and stiffness.

The circuit is just made with thick traces done manually in KiCad after calculating the required length and width. You can use the excel file included here: https://github.com/lhndo/LH-Stinger/tree/main/PCB/PI%20Bed%20Heater%20-%20200mm, which was done by [Róbert Lőrincz](https://www.orbiterprojects.com/). I picked it from his story : https://www.orbiterprojects.com/stories/story-of-the-orbitron-heated-bed-design/ . Takes a bit of time but it's not that difficult in the end.

I have ported the project to EasyEDA and you can check it out here: https://oshwlab.com/andrei6/lhs-pi-bed-heater-200x200mm

Closed 2024-12-13.

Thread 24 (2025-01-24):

gcode macro SP_FORCE_SET_LANE not defined

Bad-Hackerman, 2025-01-24:
Steps to reproduce: have the current lane not defined an try to manually override it

lhndo, 2025-01-25:
Hi, can you please give me the command and parameters along with the exact error it triggers?
Is the rest of your mmu functional, as in you have done multi color prints with it?

Bad-Hackerman, 2025-01-25:
So here is the console after selectign Tool 0:
```
$ T0
echo: SP: Sidestep Right
!! SP: Unknown current loaded LANE -1. Use SP_FORCE_SET_LANE LANE=<0...>, SP_CLEAR_ERROR_CODES, SP_UNLOAD_LANE, SP_LOAD_LANE and finally RESUME to manually change the filament.
!! SP: Print PAUSED and filament change interrupted due to previous errors. Please fix the issues before resuming
!! SP: PAUSED. Unloading LANE -1 >>>> Pending LANE 0
$ SP_FORCE_SET_LANE LANE=0
// Unknown `command:"SP_FORCE_SET_LANE"
```

While writing this I notice that the `SP_FORCE_SET_LOADED_LANE` command seems to do what `SP_FORCE_SET_LANE LANE` seems to need to do.

I haven't gotten it to work yet, just installed it yesterday, but i don't know if it is user error or a bug, but no matter the hub to sensor variable length, the filament only moves by around 20mm. When manually moving the filament with `SP_FORCE_MOVE_LANE` it moves the correct amount.

lhndo, 2025-01-25:
* SP_FORCE_SET_LANE was a typo, now it's only SP_FORCE_SET_LOADED_LANE

* I have submitted a fix that should load a lane even if nothing was loaded before

* Hub to sensor variable is just as a guide length, Moves that end up with a sensor check (homing moves) end up when the status of the sensor has changed, or when the move distance was complete

I would recommend going one by one though the macros from the guide to check that everything is operational and loads/unloads correctly  before printing

Bad-Hackerman, 2025-01-25:
I forgot to change the motor endstop pin.

Closed 2025-01-25.

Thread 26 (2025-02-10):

can not open Stinger Pico MMU - Belt Drive.3mf using cura

luanft, 2025-02-10:
I can not open this file using cura.
Can you help to convert all models to STL files?

Stinger Pico MMU - Belt Drive.3mf

Thank you for a great & tiny MMU system

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

lhndo, 2025-02-10:
Cursa doesn't support 3mf formats. I recommend downloading Prusa or Orca slicer since the rest of the MMU setup is based on that.
If you still want to bring the STL files back to Cura, after loading the 3mf in Orca you can right click and export them.
For more information please see: https://github.com/lhndo/LH-Stinger/wiki/Pico-MMU#q-where-can-i-find-the-stl-files

luanft, 2025-02-11:
@lhndo Let me try with the Orca slicer. Thank you again for a great MMU system!

Closed 2025-02-11.

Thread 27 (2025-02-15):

Any alternative for servo motor for PICO MMU

luanft, 2025-02-15:
Hi,

I'm working to build the PICO mmu. I just found that the EMAX ES3004 Servo is not available at my location.
Can I use these servos as alternative for the PICO mmu?
- Servo MG995
- Servo SG90
- Servo MG90S 360
- Servo Emax ES08MA

I'm not familiar with the servo motor. Which one can work with the PICO mmu? 360 rotation servo or 180 servo is enough?

Thank you for your help

lhndo, 2025-02-15:
Hi,

360 degrees servos are for speed controlled movement, not angle control. so they can't be used in this application.

Out of those, only the MG995 can be considered (180deg version) but you will need to consider the power delivery since the stall current draw is bigger than what a EBB 42 can supply, and you will fry the board.

The are have been some alternative servo mounts posted on the Discord server for standard size servos such as the MG995

I recommend reading this: https://github.com/lhndo/LH-Stinger/wiki/Pico-MMU#q-can-i-use-servo-x-instead

luanft, 2025-02-17:
Thank you. Seem the mount for MG995 is not available. I will design one for me and share it here.

lhndo, 2025-02-17:
Try this one: https://www.printables.com/model/1129133-stringer-pico-mmu-with-996r-servo

luanft, 2025-02-17:
This one fit to the MG995. Thank you

Closed 2025-02-17.

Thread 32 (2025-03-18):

[PICO MMU] Sync move extruder and sp_motor do not move at the same time

nbngoc93, 2025-03-18:
PICO MMU. Sync move extruder and sp_motor do not move at the same time. Test in Neptune 4 pro latest official firmware.

lhndo, 2025-03-19:
Hi, this was reported by other users which were running on an outdated klipper version from around 2021 v0.10.0.
What version are you on? Can you please try updating to v0.12.0 +

nbngoc93, 2025-03-20:
I think I am on v0.10.xxx. I will try to upgrade it to v0.12.0

Closed 2025-03-20.

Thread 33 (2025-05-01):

MACRO ERROR

WeslenPy, 2025-05-01:
Error evaluating 'gcode_macro _SP_MOTOR:gcode': ZeroDivisionError: float division by zero

problem after set variable variable_dist_sensor_to_synced_move for 3

lhndo, 2025-05-02:
Like I wrote before, the synced move distance is extremely short. Try increasing it along with decreasing sensor_safe_move and backlash. Let me know if that still happens then.
I will leave the error trigger since it signals an configuration issue, and I consider that to be better than masking the division by 0

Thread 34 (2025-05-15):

Alterative Servos

mike2194, 2025-05-15:
Just wanted to share alternate servo I used with [testing] success:
https://www.amazon.com/dp/B0DDNLR665

It seems the only requirement is force capability and [screw mount distance](https://m.media-amazon.com/images/I/71vY0iy6arL._AC_SL1500_.jpg) (34mm)

lhndo, 2025-05-16:
Good to know, thanks for the information @mike2194!

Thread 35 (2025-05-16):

Cam Shaft Position Changing After Every Restart.

SalsShadow, 2025-05-16:
When I set the servo positions they always change each time I turn the printer back on, any idea why?

I check the troubleshooting section and didn't see anything that would help me fix it.

lhndo, 2025-05-17:
The servo resets itself when is powered then the pico code sets it to home (0) positions.
If the lane angle doesn't match between sessions then you might have a mechanical issue where the belt or the pulleys are slipping

SalsShadow, 2025-05-17:
The belt isn't slipping at all, it is well tensioned and I have watched it. It does not slip at all.

Closed 2025-06-02.

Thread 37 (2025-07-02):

Alternative servo motor

madmonkey0, 2025-07-02:
Which are the alternative servo and with mg996r what will be the connection

lhndo, 2025-07-02:
I only did long term testing on the BOM spec servo, and that's the only one recommended officially at the moment.

Closed 2025-07-05.

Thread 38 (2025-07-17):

Bigger bed

DiomedesDominguez, 2025-07-17:
Hi, I considere 235 mm^2 way below of this excellent machine should have as print base area, so If I want to use something more commercially available like the Voron 2.4 250 bed, which parts should I modify to allow it?

lhndo, 2025-07-17:
Hi, the Stinger is designed to be compatible with a 235mm^2 ender 3 heated bed, so you can use that.
Voron beds are not suited since they weigh a couple of kg.

Closed 2025-07-17.

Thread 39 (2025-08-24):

[PICO MMU] Sync move extruder and sp_motor do not move at the same time

dacan2810, 2025-08-24:
Klipper version: v0.13.0-229-g3aadda6f
Pico MMU config 0.9.2
I was inspected that now when unload. extruder and sp motor move in order ( sp motor grab filamane then stop, then extruder unload filament).
=> Sync move fail when unload

i see error at code below. when i switched to legacy mode. extruder and sp motor move togeter
when normal it move in order => fail which mean _SP_MOTOR  and FORCE_MOVE not working same time
I think because klipper changed. because i switch back to 0.9.1 (which is already work for me before) and it still happaned

     {% if legacy == 1 %}
        M83
        G92 E0
        _SP_MOTOR STOP=0 SYNC=0 SPEED={sync_speed} ACCEL={sp.motor_accel} DIST={sync_dist}
        G0 E{sync_dist} F{60*sync_speed}
      {% else %}
        _SP_MOTOR STOP=0 SYNC=0 SPEED={sync_speed} ACCEL={sp.motor_accel} DIST={sync_dist}
        FORCE_MOVE STEPPER=extruder VELOCITY={sync_speed} ACCEL={sp.motor_accel} DISTANCE={sync_dist}
      {% endif %}

lhndo, 2025-08-24:
Hi @dacan2810, thanks for the report!
I assume that's that the latest version to date

If so, it's very likely that the latest klipper changes also broke the way the sync manual stepper mode works, in particular to this command:

`MANUAL_STEPPER STEPPER=sp_motor ENABLE=1 SET_POSITION=0 SPEED={speed} ACCEL={accel} MOVE={dist} SYNC=1`

There was an attempt to fix the manual stepper in, but it addressed a more general issue: https://github.com/Klipper3d/klipper/commit/91b5e8e9425b5063c8a5bab9358d4c45c0e3430c

You can try rolling back to this cl:

```
cd ~/klipper
sudo systemctl stop klipper
git reset --hard 17ce45d2
sudo systemctl start klipper
```

dacan2810, 2025-08-24:
Hi @lhndo. Thanks for reply
I can confirm it happened on lasted klipper.
Following your guide, i rollback to 17ce45d2 and it work fine with non-legacy mode.
As soon as update to lasted, it still happen.
It take me days try to fixing hotend and debug :D

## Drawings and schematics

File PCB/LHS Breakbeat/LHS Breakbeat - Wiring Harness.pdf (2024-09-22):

# SENSORS

## WIRING HARNESS V 1.4

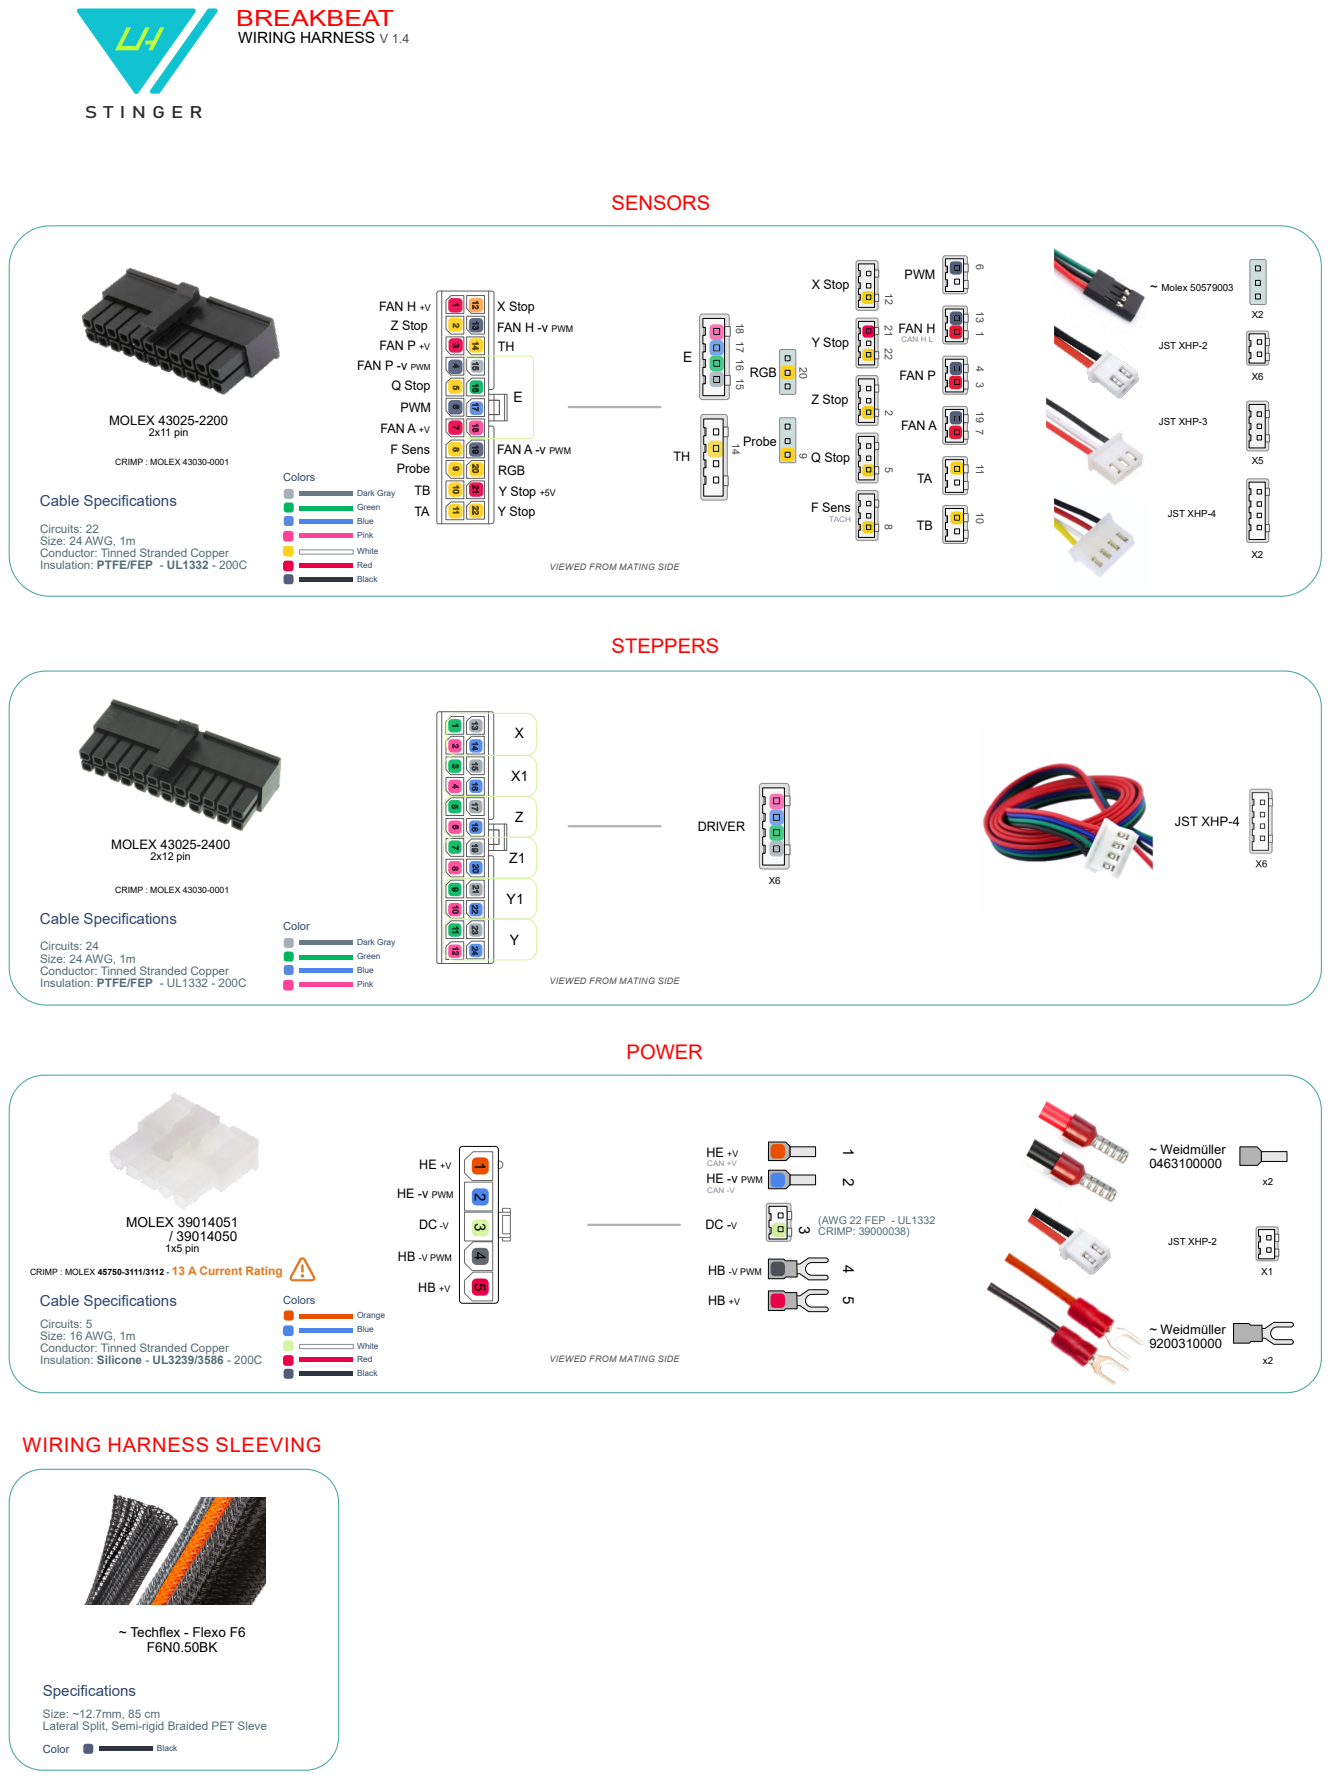
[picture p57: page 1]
Specifications; Color; Black; ~ Techflex - Flexo F6 F6N0.50BK; POWER; ~ Weidmüller 0463100000; ~ Weidmüller 9200310000; JST XHP-2; CAN +V; CAN -V; HE -v PWM; HB -V PWM; Colors; Orange; Blue; White; Red; Cable Specifications; MOLEX 39014051 / 39014050 1x5 pin; (AWG 22 FEP - UL1332 CRIMP: 39000038); MOLEX 43025-2400 2x12 pin; CRIMP : MOLEX 43030-0001; Pink; Dark Gray; Green; STEPPERS; DRIVER; MOLEX 43025-2200 2x11 pin; X Stop; Y Stop; Z Stop; Q Stop; PWM; FAN H -v PWM; FAN P -v PWM; FAN A -v PWM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

Circuits: 22
Size: 24 AWG, 1m
Conductor: Tinned Stranded Copper

Circuits: 24
Insulation: PTFE/FEP - UL1332 - 200C

VIEWED FROM MATING SIDE

CRIMP : MOLEX 45750-3111/3112 - 13 A Current Rating

Circuits: 5
Size: 16 AWG, 1m
Insulation: Silicone - UL3239/3586 - 200C

WIRING HARNESS SLEEVING

Size: ~12.7mm, 85 cm
Lateral Split, Semi-rigid Braided PET Sleve

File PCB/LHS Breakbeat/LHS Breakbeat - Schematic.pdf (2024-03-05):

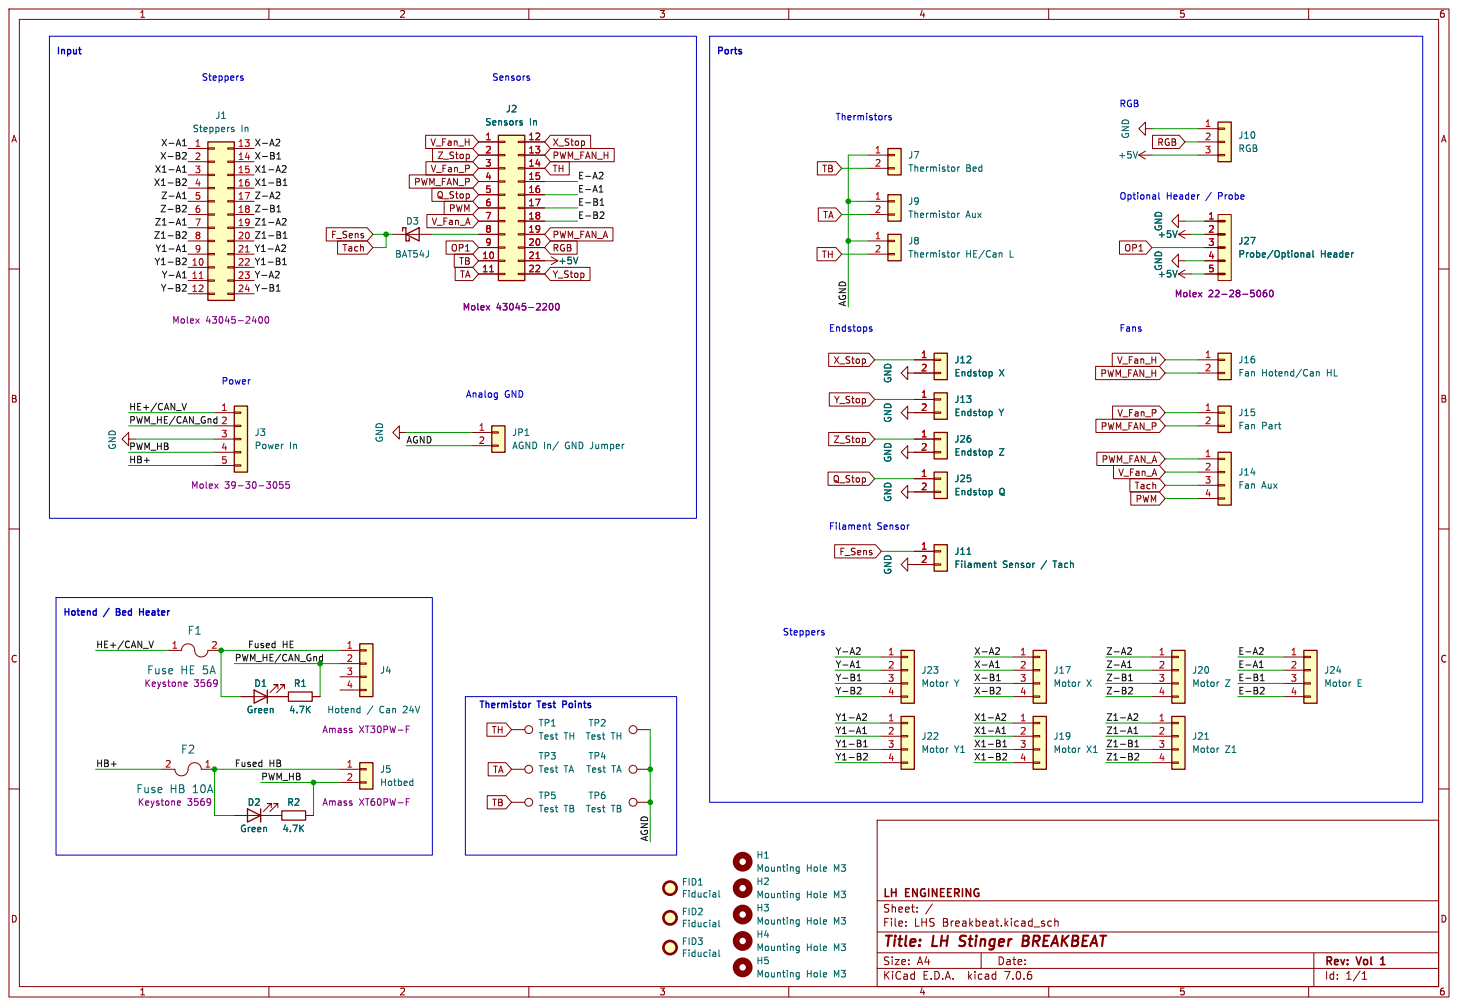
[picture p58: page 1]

Steppers Hotend / Bed Heater

Id: 1/1 Title: LH Stinger BREAKBEAT

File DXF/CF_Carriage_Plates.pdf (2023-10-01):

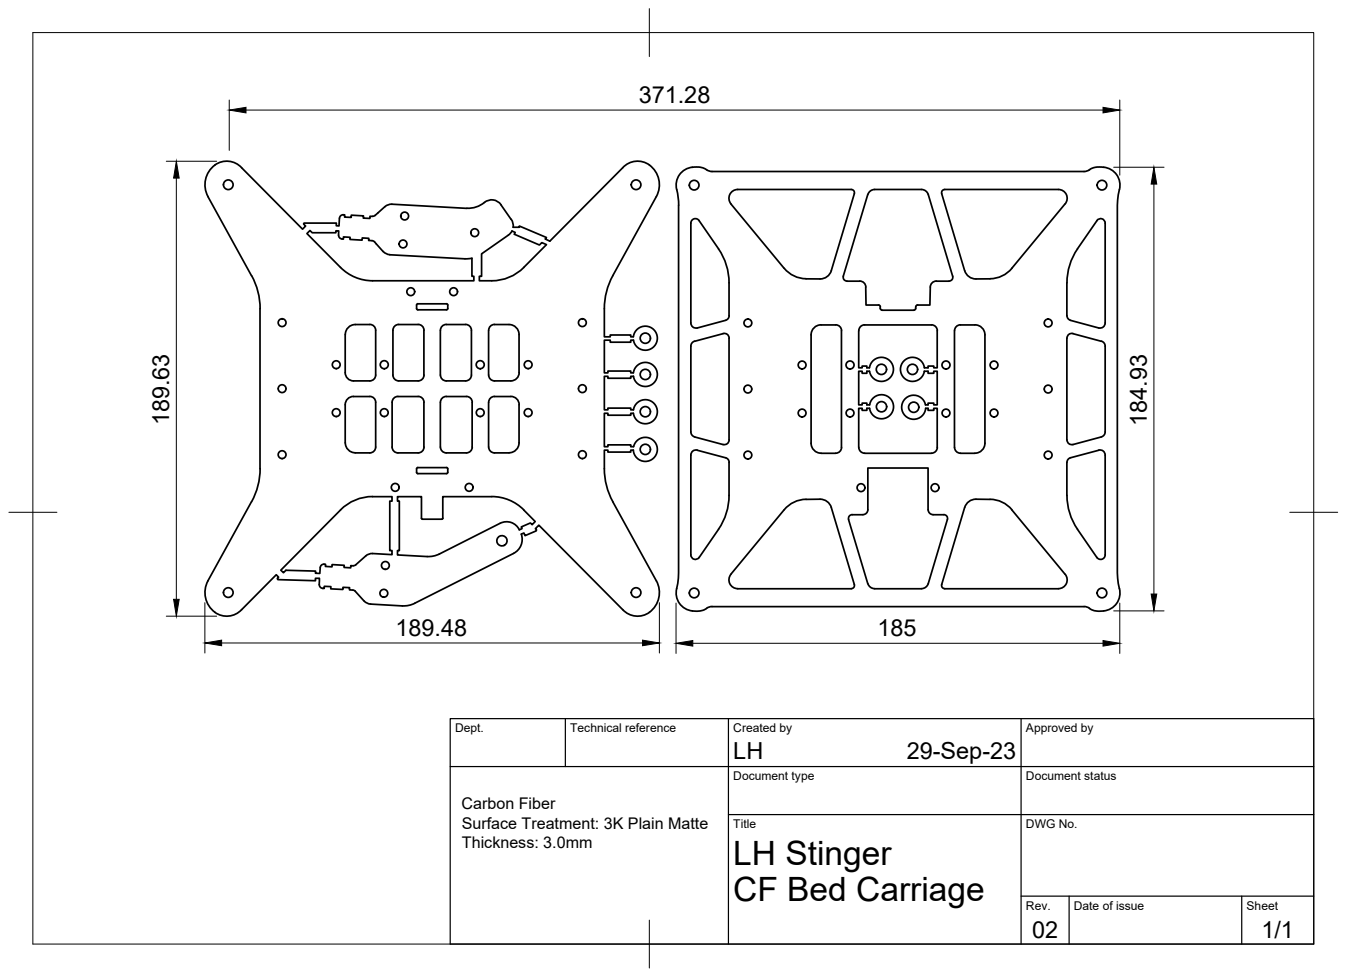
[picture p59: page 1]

Dept. | Technical reference | Created by LH 29-Sep-23 | Approved by

Carbon Fiber Surface Treatment: 3K Plain Matte Thickness: 3.0mm | | Document type | Document status

Title LH Stinger CF Bed Carriage | DWG No.

Rev. 02 | Date of issue | Sheet 1/1

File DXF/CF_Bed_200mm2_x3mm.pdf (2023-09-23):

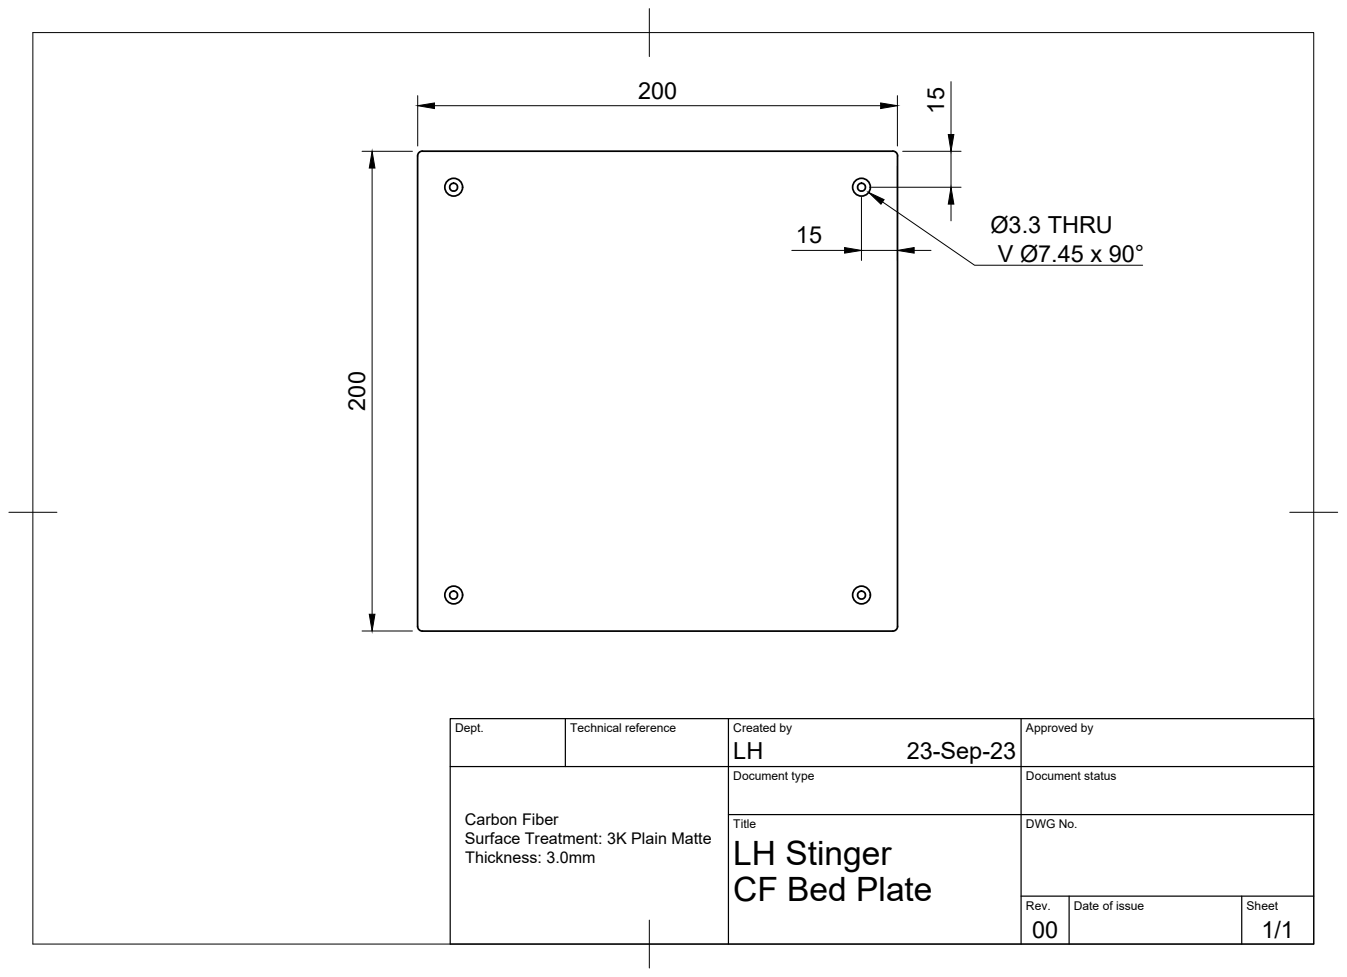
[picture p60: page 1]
Ø3.3 THRU V Ø7.45 x 90°

Dept. | Technical reference | Created by LH 23-Sep-23 | Approved by

Carbon Fiber Surface Treatment: 3K Plain Matte Thickness: 3.0mm | | Document type | Document status

Title LH Stinger CF Bed Plate | DWG No.

Rev. 00 | Date of issue | Sheet 1/1

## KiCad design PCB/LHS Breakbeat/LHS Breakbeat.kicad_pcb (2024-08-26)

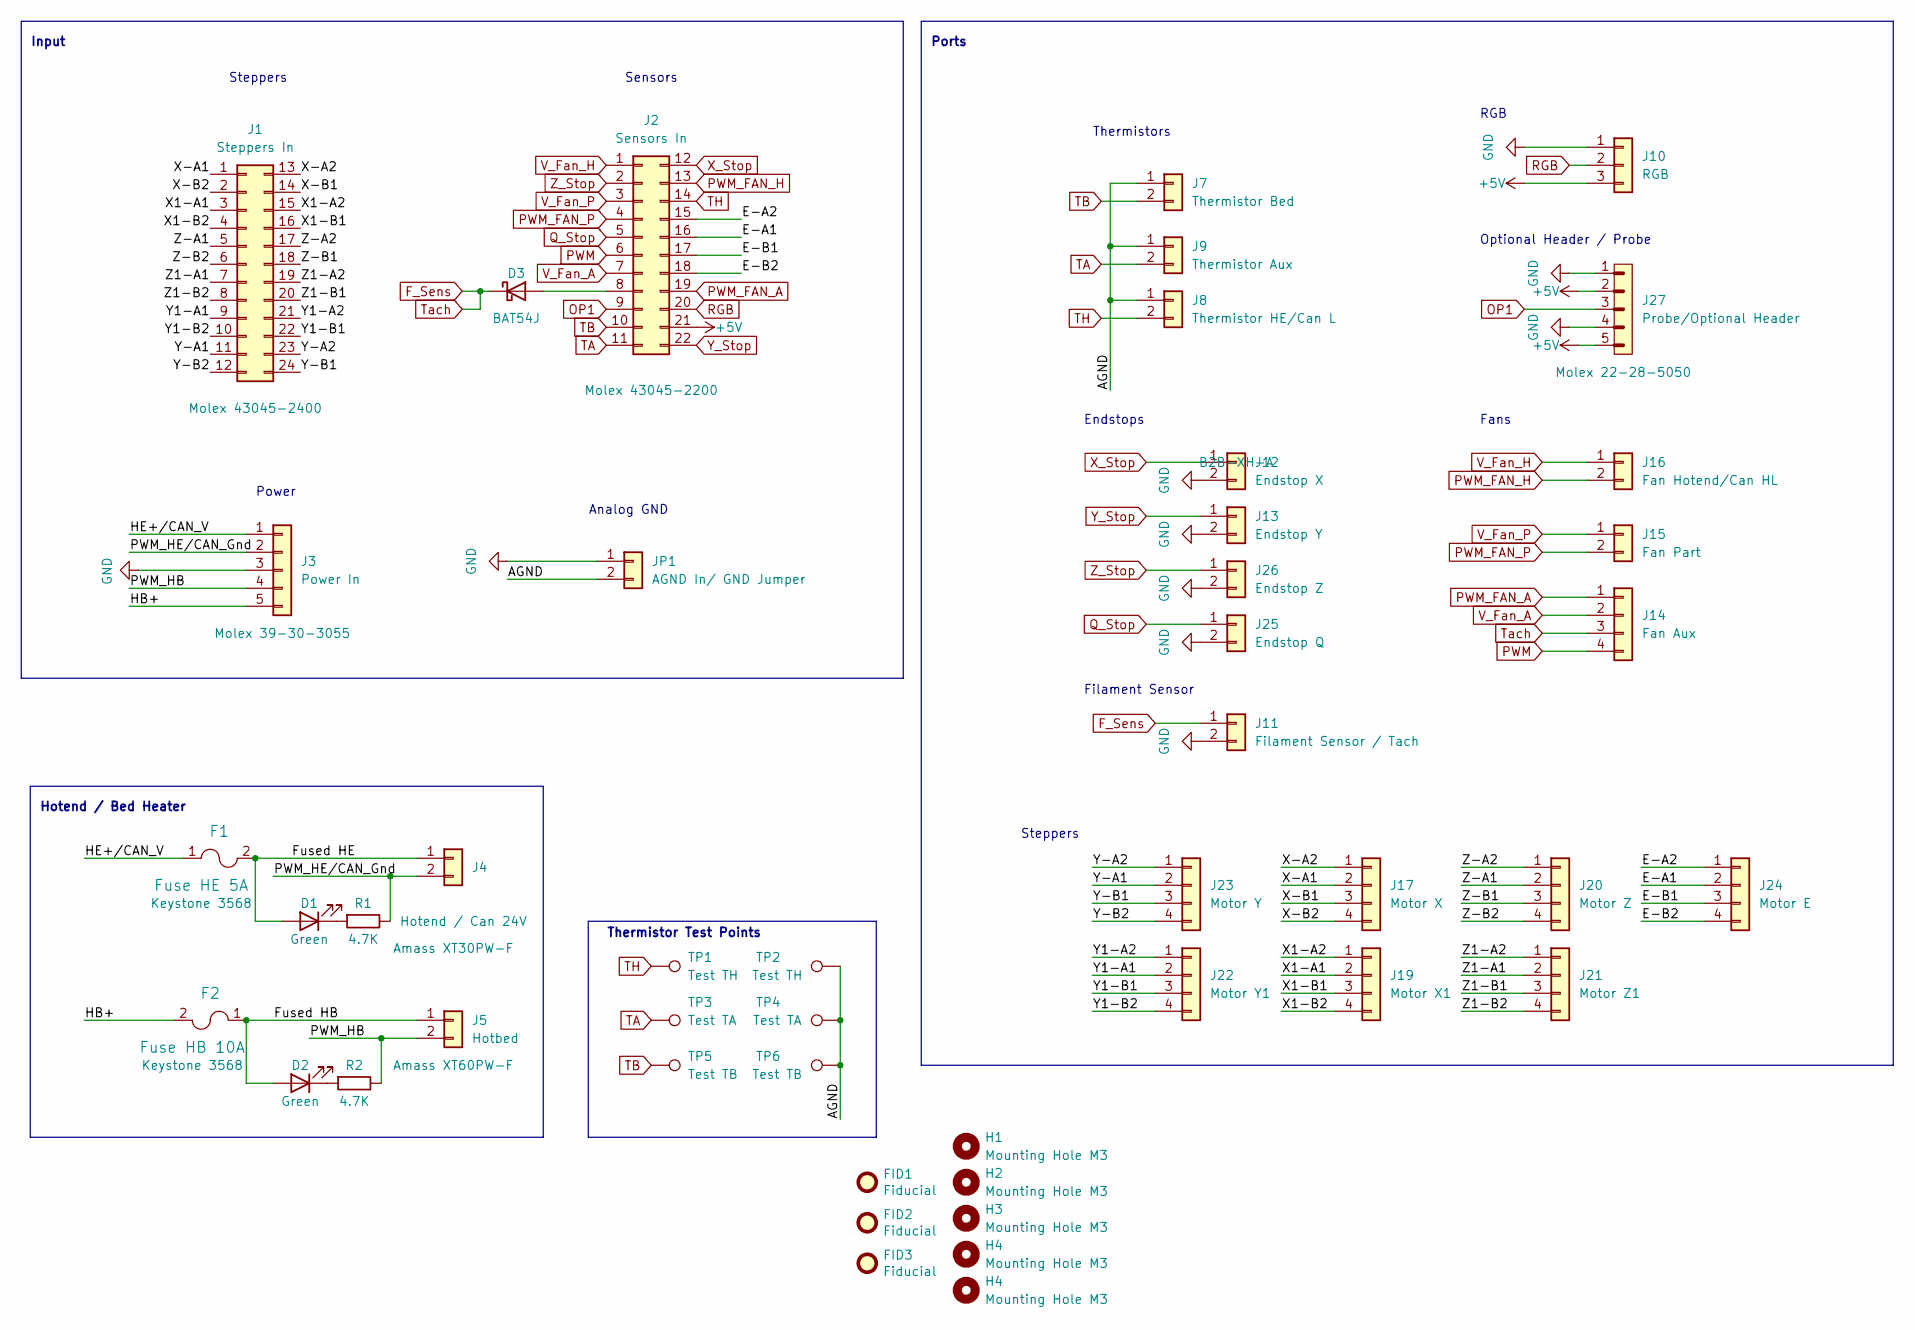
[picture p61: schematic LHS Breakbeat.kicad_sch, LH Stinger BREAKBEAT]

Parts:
D1, D2: Green; LED_0805_2012Metric_Pad1.15x1.40mm_HandSolder; LCSC C2297
D3: BAT54J; D_SOD-323F; LCSC C130415
F1: Fuse HE 5A; Fuseholder_Blade_Mini_Keystone_3568; LCSC C3206956
F2: Fuse HB 10A; Fuseholder_Blade_Mini_Keystone_3568; LCSC C3206956
FID1, FID2, FID3: Fiducial; Fiducial_1.5mm_Mask3mm
H1, H2, H3, H4: Mounting Hole M3; MountingHole_3.2mm_M3_DIN965_Pad
J1: Steppers In; 0430452400; LCSC C277384
J2: Sensors In; 43045-22_00,01,02,10_; LCSC C127339
J3: Power In; 39303055; LCSC C485326
J4: Hotend / Can 24V; XT30PWF; LCSC C2913282
J5: Hotbed; AMASS_XT60PW-F_1x02_P7.20mm_Horizontal; LCSC C428722
J7: Thermistor Bed; JST_XH_B2B-XH-A_1x02_P2.50mm_Vertical; LCSC C5258883
J8: Thermistor HE/Can L; JST_XH_B2B-XH-A_1x02_P2.50mm_Vertical; LCSC C5258883
J9: Thermistor Aux; JST_XH_B2B-XH-A_1x02_P2.50mm_Vertical; LCSC C5258883
J10: RGB; JST_XH_B3B-XH-A_1x03_P2.50mm_Vertical; LCSC C492457
J11: Filament Sensor / Tach; JST_XH_B2B-XH-A_1x02_P2.50mm_Vertical; LCSC C5258883
J12: Endstop X; JST_XH_B2B-XH-A_1x02_P2.50mm_Vertical; LCSC C5258883
J13: Endstop Y; JST_XH_B2B-XH-A_1x02_P2.50mm_Vertical; LCSC C5258883
J14: Fan Aux; JST_XH_B4B-XH-A_1x04_P2.50mm_Vertical; LCSC C709375
J15: Fan Part; JST_XH_B2B-XH-A_1x02_P2.50mm_Vertical; LCSC C5258883
J16: Fan Hotend/Can HL; JST_XH_B2B-XH-A_1x02_P2.50mm_Vertical; LCSC C5258883
J17: Motor X; JST_XH_B4B-XH-A_1x04_P2.50mm_Vertical; LCSC C709375
J19: Motor X1; JST_XH_B4B-XH-A_1x04_P2.50mm_Vertical; LCSC C709375
J20: Motor Z; JST_XH_B4B-XH-A_1x04_P2.50mm_Vertical; LCSC C709375
J21: Motor Z1; JST_XH_B4B-XH-A_1x04_P2.50mm_Vertical; LCSC C709375
J22: Motor Y1; JST_XH_B4B-XH-A_1x04_P2.50mm_Vertical; LCSC C709375
J23: Motor Y; JST_XH_B4B-XH-A_1x04_P2.50mm_Vertical; LCSC C709375
J24: Motor E; JST_XH_B4B-XH-A_1x04_P2.50mm_Vertical; LCSC C709375
J25: Endstop Q; JST_XH_B2B-XH-A_1x02_P2.50mm_Vertical; LCSC C5258883
J26: Endstop Z; JST_XH_B2B-XH-A_1x02_P2.50mm_Vertical; LCSC C5258883
J27: Probe/Optional Header; PinHeader_1x05_P2.54mm_Vertical; LCSC C2935911
JP1: AGND In/ GND Jumper; PinHeader_1x02_P2.54mm_Vertical; LCSC C2685195
R1, R2: 4.7K; R_0805_2012Metric_Pad1.20x1.40mm_HandSolder; LCSC C17673
TP1, TP2: Test TH; TestPoint_Pad_D2.0mm
TP3, TP4: Test TA; TestPoint_Pad_D2.0mm
TP5, TP6: Test TB; TestPoint_Pad_D2.0mm

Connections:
+5V: J2.21, J10.3, J27.2, J27.5
/AGND: J7.1, J8.1, J9.1, JP1.2, TP2.1, TP4.1, TP6.1
/E-A1: J2.16, J24.2
/E-A2: J2.15, J24.1
/E-B1: J2.17, J24.3
/E-B2: J2.18, J24.4
/Fused HB: D2.2 (A), F2.1, J5.1
/Fused HE: D1.2 (A), F1.2, J4.1
/HB+: F2.2, J3.5
/HE+/CAN_V: F1.1, J3.1
/PWM_HB: J3.4, J5.2, R2.2
/PWM_HE/CAN_Gnd: J3.2, J4.2, R1.2
/X1-A1: J1.3, J19.2
/X1-A2: J1.15, J19.1
/X1-B1: J1.16, J19.3
/X1-B2: J1.4, J19.4
/X-A1: J1.1, J17.2
/X-A2: J1.13, J17.1
/X-B1: J1.14, J17.3
/X-B2: J1.2, J17.4
/Y1-A1: J1.9, J22.2
/Y1-A2: J1.21, J22.1
/Y1-B1: J1.22, J22.3
/Y1-B2: J1.10, J22.4
/Y-A1: J1.11, J23.2
/Y-A2: J1.23, J23.1
/Y-B1: J1.24, J23.3
/Y-B2: J1.12, J23.4
/Z1-A1: J1.7, J21.2
/Z1-A2: J1.19, J21.1
/Z1-B1: J1.20, J21.3
/Z1-B2: J1.8, J21.4
/Z-A1: J1.5, J20.2
/Z-A2: J1.17, J20.1
/Z-B1: J1.18, J20.3
/Z-B2: J1.6, J20.4
F_Sens: D3.1 (K), J11.1, J14.3
GND: J3.3, J10.1, J11.2, J12.2, J13.2, J25.2, J26.2, J27.1, J27.4, JP1.1
unnamed: D1.1 (K), R1.1
unnamed: D2.1 (K), R2.1
unnamed: D3.2 (A), J2.8
OP1: J2.9, J27.3
PWM: J2.6, J14.4
PWM_FAN_A: J2.19, J14.1
PWM_FAN_H: J2.13, J16.2
PWM_FAN_P: J2.4, J15.2
Q_Stop: J2.5, J25.1
RGB: J2.20, J10.2
TA: J2.11, J9.2, TP3.1
TB: J2.10, J7.2, TP5.1
TH: J2.14, J8.2, TP1.1
V_Fan_A: J2.7, J14.2
V_Fan_H: J2.1, J16.1
V_Fan_P: J2.3, J15.1
X_Stop: J2.12, J12.1
Y_Stop: J2.22, J13.1
Z_Stop: J2.2, J26.1

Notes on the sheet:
Fans
Analog GND
Power
Endstops
Input
Hotend / Bed Heater
Steppers
Ports
Thermistors
Optional Header / Probe
Filament Sensor
Thermistor Test Points
Sensors
RGB

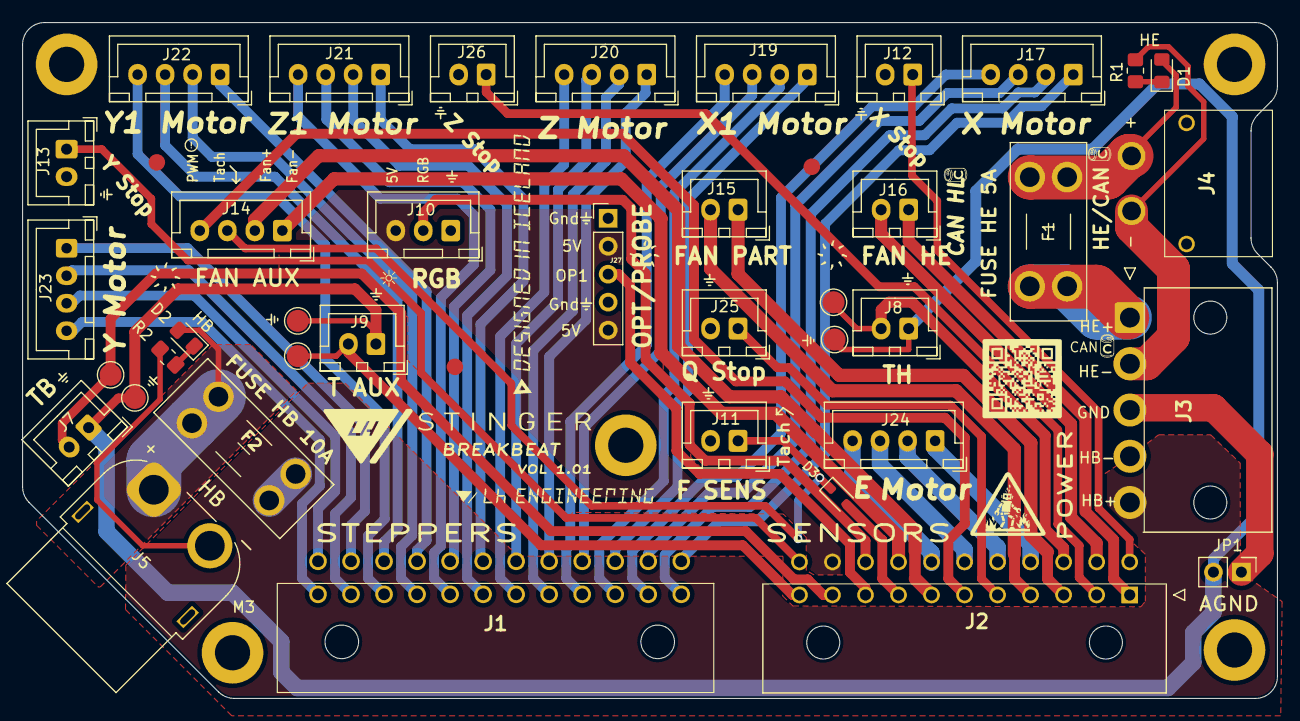
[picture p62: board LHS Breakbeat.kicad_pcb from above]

Board: 2 copper layers, 114.0 x 61.4 mm, 47 parts (0 on the bottom side), 57 nets.

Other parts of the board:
H5: Mounting Hole M3; MountingHole_3.2mm_M3_DIN965_Pad

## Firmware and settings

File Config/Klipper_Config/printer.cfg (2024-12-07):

###________________________________________________
#    __          __  __________    __  ___   __  __  
#   / /  /\  /\ / _\/__   \_   \/\ \ \/ _ \ /__\/__\ 
#  / /  / /_/ / \ \   / /\// /\/  \/ / /_\//_\ / \// 
# / /__/ __  /  _\ \ / //\/ /_/ /\  / /_\\//__/ _  \ 
# \____|/ /_/   \__/ \/ \____/\_\ \/\____/\__/\/ \_/                           
         
### BTT Octopus Pro 1.1 - STM32H723

### BTT Octopus Pro Firmware Guide https://github.com/bigtreetech/BIGTREETECH-OCTOPUS-V1.0/blob/master/Firmware/Klipper/README.md
### Flash with (H723 ver. only):
### "128KiB bootloader" and a "25Mhz crystal"
### USB Communication interface (PA11/PA12)


###______________  Documentation:  ______________

### Klipper Setup: https://github.com/lhndo/LH-Stinger/tree/main/Config/Klipper_Config
### Macros: https://github.com/lhndo/LH-Stinger/wiki/Macros
### Tuning Guide: https://github.com/lhndo/LH-Stinger/wiki/Tuning


###______________  Configuration Includes  ______________

[include mainsail.cfg]   # Mainsail or Fluid configuration choice, depending on your Klipper installation
# [include fluidd.cfg]

[include steppers.cfg]
# [include steppersfast.cfg]  # High performance configuration only meant for extreme tests and prints (above 700mm/s at very high accels). Choose one or the other.

[include quickdrawprobe.cfg]   # Quickdraw Probe Extension by Daalegard. For instructions please see quickdrawprobe.cfg 
# [include adxl.cfg]   # Enable when connecting an ADXL device and change the parameters in the .cfg 

[include reshelper.cfg]   # Reshelper https://github.com/lhndo/ResHelper/tree/accel_per_hz

[include mymacros.cfg]   # Macros



###__________________  MCU  ____________________

[mcu]
serial: /dev/serial/by-id/usb-Klipper_stm32h723xx_3A0010001151313236343430-if00    # To find your USB serial addres run: ls /dev/serial/by-id/*


###_______________  Printer  ___________________

[printer]
kinematics: cartesian
max_velocity: 1000
max_accel: 5000           # Set for homing moves. Adjust accel per feature in the slicer
minimum_cruise_ratio: 0.0
max_z_velocity: 70
max_z_accel: 800
square_corner_velocity: 15.0


###_______________  Steppers  ___________________

[stepper_x]  ;  Motor 6
step_pin: PE2
dir_pin: PE3 
enable_pin: !PD4
endstop_pin: PG13
full_steps_per_rotation: 200
rotation_distance: 40
position_endstop: 0      # Do not change. The bed location is defined in the slicer according to the documentation: https://github.com/lhndo/LH-Stinger/wiki/Macros#bed-origin
position_min: 0          # Do not change
position_max: 254
homing_speed: 80
homing_retract_dist: 0

[stepper_y]   ;  Motor 5
step_pin: PC13
dir_pin: PF0
enable_pin: !PF1
endstop_pin: PG14
full_steps_per_rotation: 200
rotation_distance: 40
position_endstop: 0      # Do not change 
position_min: 0          # Do not change
position_max: 252
homing_speed: 80
homing_retract_dist: 0

[stepper_y1]   ;  Motor 4
step_pin: PF9
dir_pin: !PF10
enable_pin: !PG2
endstop_pin: PG14
full_steps_per_rotation: 200
rotation_distance: 40

[stepper_z]   ;  Motor 2
step_pin: PF11
dir_pin: PG3
enable_pin: !PG5
endstop_pin: probe:z_virtual_endstop
full_steps_per_rotation: 200
rotation_distance: 40
gear_ratio: 80:20
position_min: -20
position_max: 196
homing_speed: 10
second_homing_speed: 4
homing_retract_dist:3

[stepper_z1]  ;  Motor 0
step_pin: PF13
dir_pin: !PF12
enable_pin: !PF14
full_steps_per_rotation: 200
rotation_distance: 40
gear_ratio: 80:20

# [stepper_6]  ;  Motor 3
# step_pin: PG4
# dir_pin: PC1
# enable_pin: !PA2

# [stepper_7]   ;  Motor 7
# step_pin: PE6
# dir_pin: PA14
# enable_pin: !PE0
# endstop_pin: PG11


[probe]
z_offset: 7 # calibrate with probe_calibrate command. Remember to remove the probe from the toolhead. After calibrating and saving this will be automatically commented. 


###_______________  Extruder/Bed  ___________________

[extruder]   ;  Motor 1
step_pin: PG0
dir_pin: PG1
enable_pin: !PF15

# heater_pin: PA0    # Disable when the hotend thermistor is connected though MAX31865 
# sensor_type: PT1000
# sensor_pin: PF4

# ----- MAX31865 Configuration -----
heater_pin: PA0 # HE0
sensor_type: MAX31865
spi_bus: spi1
sensor_pin: PF8
rtd_nominal_r: 1000
rtd_num_of_wires: 2
rtd_reference_r: 4300
rtd_use_50Hz_filter: True
#-----------------------------------

smooth_time: 1.0
rotation_distance: 4.716  # Measured. Factory Default: 4.637 
full_steps_per_rotation: 200
min_temp: 0
max_temp: 310
min_extrude_temp: 170
nozzle_diameter: 0.500
filament_diameter: 1.750
max_extrude_cross_section: 5
max_extrude_only_distance: 1000.0
max_extrude_only_velocity: 120
max_extrude_only_accel: 2800
instantaneous_corner_velocity: 5
pressure_advance: 0.025
pressure_advance_smooth_time: 0.02
control: pid
pid_Kp: 27.034
pid_Ki: 1.877
pid_Kd: 97.321


[heater_bed]
heater_pin: PA1
sensor_pin: PF3 # TB
sensor_type: Generic 3950
smooth_time: 1
min_temp: 0
max_temp: 120
control: pid
pid_Kp: 58.277
pid_Ki: 3.108
pid_Kd: 273.173


###_______________  Fans  ___________________

# Fan 1 - Hotend Cooling Fan
[heater_fan hotend_fan]
pin: PA8
heater: extruder
heater_temp: 70.0
kick_start_time: 0.500
hardware_pwm: False
cycle_time: 0.01
fan_speed: 1.0

# Fan 2 - Part Cooling Fan
[fan]
pin: PE5
cycle_time: 0.01
kick_start_time: 0.2
hardware_pwm: False

#  Fan 3 - Optional Auxiliary Fan
[fan_generic aux]
pin:PD12
cycle_time: 0.017
hardware_pwm: False
kick_start_time: 0.2
off_below: 0.15

[multi_pin ebox]
pins: PD13

# Fan 4 - Ebox
[controller_fan ebox_stm32] 
pin:multi_pin:ebox
kick_start_time: 0.2
stepper: stepper_y
cycle_time: 0.01
idle_timeout: 30
idle_speed: 1.0
off_below: 0.5


###_______________  Temperature Sensors  ___________________

# [temperature_sensor external] ; Optional external temperature sensor
# sensor_pin:PF5
# sensor_type: Generic 3950
# min_temp: 0
# max_temp: 300

[temperature_sensor MCU]
sensor_type: temperature_mcu
min_temp: 0
max_temp: 100

[temperature_sensor PI]
sensor_type: temperature_host
min_temp: 0
max_temp: 100

###_______________  Modules  _____________________

[idle_timeout]
timeout: 600
gcode:
  {% if printer.pause_resume.is_paused %}
    M118 Idle timeout while paused, turning off hotend
    SET_HEATER_TEMPERATURE HEATER=extruder TARGET=0
  {% else %}
    M118 Idle timeout, turning off hotend and disabling steppers
    TURN_OFF_HEATERS
    M84
  {% endif %}

[exclude_object]

[respond]

[resonance_holder]
accel_per_hz: 180

[display_status]

[force_move]
enable_force_move: true

[respond]
default_type: echo
default_prefix:

[gcode_arcs]
resolution: 0.1


#*# <---------------------- SAVE_CONFIG ---------------------->
#*# DO NOT EDIT THIS BLOCK OR BELOW. The contents are auto-generated.
#*#

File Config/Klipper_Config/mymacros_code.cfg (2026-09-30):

##### LH Stinger User Macros Code #####


[virtual_sdcard]
path: ~/printer_data/gcodes
on_error_gcode: 
  RESPOND TYPE=command MSG='Vritual SD error triggered. Starting CANCEL_PRINT'
  CANCEL_PRINT



[gcode_macro CANCEL_PRINT] 
rename_existing: CANCEL_PRINT_BASE
gcode:
  PRINT_END
  CANCEL_PRINT_BASE



[gcode_macro RESET]
description: RESTART
gcode:
  RESTART




##### Slicer Macros #####

[gcode_macro PRINT_START_LHS]
gcode:        
    # Parameters
    {% set bedtemp = params.BED|int %}
    {% set hotendtemp = params.HOTEND|int %}
    {% set autopurge = params.AUTOPURGE| default(0) | int %}
    {% set automesh = params.AUTOMESH| default(0) | int %}
    {% set quietmode = params.QUIETMODE| default(0) | int %}
    {% set client = printer['gcode_macro _CLIENT_VARIABLE'] %}
    {% set rt = printer['gcode_macro _CLIENT_VARIABLE_RUNTIME'] %}

    _CHECK_SETTINGS_VERSION_LHS # Settings file version check

    {% if client.stop_bg_services == True %}
      _STOP_CRON  # Stop background host scheduled tasks
    {% endif %}

    SAVE_GCODE_STATE NAME=print_start
    SET_GCODE_VARIABLE MACRO=_CLIENT_VARIABLE_RUNTIME VARIABLE=end_park VALUE=False
    G90 
    M83

    ## If Y axis homed, move bed to center to avoid heating over the motors
    {% if "y" in printer.toolhead.homed_axes %}
      {% set home = printer.configfile.settings.xz_dockable_probe.home_xy_position.split(',') %}
       G1 Y{home[1]} F{150*60}   
    {% endif %}

    # cleanup from previous if needed
    M104 S{0}

    M400
    RESPOND TYPE=command MSG='Heating Bed. Please wait'
    
    {% if client.boost_bed_heat_time == True and bedtemp > 24 %}
      M140 S{bedtemp+10} # Heat bed 
      TEMPERATURE_WAIT SENSOR=heater_bed MINIMUM={bedtemp-7} MAXIMUM={bedtemp+10} 
      M140 S{bedtemp}
    {% else %}
      M190 S{bedtemp} # Heat bed and wait
    {% endif %}

    M104 S{hotendtemp-60} # Pre-heat hotend to target-60C to prevent oozing 
    
    RESPOND TYPE=command MSG='Homing printer'
    PROBE_LOCK
    SET_VELOCITY_LIMIT VELOCITY={client.velocity_start} ACCEL={client.accel_start} # Lower velocity for setup moves
    G28 # home
    Z_TILT_ADJUST SAMPLES=1 RETRY_TOLERANCE=0.025
    Z_TILT_ADJUST SAMPLES=1
    G28 Z
    
    {% set profiles = printer.bed_mesh.profiles %}
    
    {% if automesh == 0 or client.foce_default_bed_mesh == True %}
      RESPOND TYPE=command MSG='Automesh OFF. Loading saved mesh'
    
      {% if client.use_multi_bed_mesh_profiles == True %}
        {% if bedtemp > 95 %}
          {% set target = '105' %}
        {% elif bedtemp > 69 %}
          {% set target = '75' %}
        {% else %}
          {% set target = 'default' %}
        {% endif %}
      {% else %}
        {% set target = 'default' %}
      {% endif %}
    
      {% if target in profiles %}
        BED_MESH_PROFILE LOAD={target}
      {% else %}
        RESPOND TYPE=error MSG='Bed mesh profile "{target}" not found, calibrating instead'
        BED_MESH_CLEAR
        BED_MESH_CALIBRATE ADAPTIVE=1
        SET_GCODE_VARIABLE MACRO=_CLIENT_VARIABLE_RUNTIME VARIABLE=automeshed VALUE=True
        G28 Z
      {% endif %}
    
    {% elif automesh == -1 %}
      RESPOND TYPE=command MSG='Automesh disabled. Continuing'
      BED_MESH_CLEAR
    {% else %}
      BED_MESH_CLEAR
      BED_MESH_CALIBRATE ADAPTIVE=1
      SET_GCODE_VARIABLE MACRO=_CLIENT_VARIABLE_RUNTIME VARIABLE=automeshed VALUE=True
      G28 Z
    {% endif %}
    
    PROBE_UNLOCK
    PROBE_DETACH
    
    G1 X{client.nozzle_heat_x} Y{client.nozzle_heat_y} Z{client.nozzle_heat_z} F3000  # Safe spot to heat up nozzle

    {% if rt.start_change == False %}
      RESPOND TYPE=command MSG='Heating Hotend. Please wait'
      M109 S{hotendtemp} # Heat hotend and wait
    {% endif %}
    
    #Quiet Mode
    {% if quietmode == 1 %}
      Qmode
    {% endif %}
    
    M400
    {% if autopurge == 0 or rt.start_change == True %}
      G1 E{client.my_end_retract} F{10*60} # Prime nozzle
    {% else %}
      _PURGE_LINE
    {% endif %}
    
    SET_VELOCITY_LIMIT VELOCITY={printer.configfile.settings.printer.max_velocity} ACCEL={printer.configfile.settings.printer.max_accel}  # Restore velocity to default
    G92 E0 # Reset Extruder
    M400
    RESPOND TYPE=command MSG='Print Started'
    RESTORE_GCODE_STATE NAME=print_start
    G90
    
    {% if rt.start_change == True %}
      RESPOND TYPE=command MSG='Filament Change Trigger. Please wait for unloading!'

      {% if rt.start_load_temp == 0 %}
          SET_GCODE_VARIABLE MACRO=_CLIENT_VARIABLE_RUNTIME VARIABLE=start_load_temp VALUE={hotendtemp}
      {% endif %}

      FILAMENT_UNLOAD TEMP={rt.start_unload_temp}
      M400
      RESPOND TYPE=command MSG='Pausing!'
      PAUSE X={client.nozzle_heat_x} Y={client.nozzle_heat_y} Z_MIN={client.change_z_min}
    {% endif %}


[gcode_macro PRINT_END]
gcode:
    TURN_OFF_HEATERS # Safety call in case of any other move fails
    
    {% set client = printer['gcode_macro _CLIENT_VARIABLE'] %}
    {% set rt = printer['gcode_macro _CLIENT_VARIABLE_RUNTIME'] %}
    {% set can_extrude = True if printer.toolhead.extruder == ''           # no extruder defined in config
                else printer[printer.toolhead.extruder].can_extrude %}     # status of active extruder
    
    G90 # Absolute Position
    M83 # Relative Extrude
    G92 E0 # Reset Extruder

    {% if "xyz" in printer.toolhead.homed_axes and can_extrude == True %}
      G1 E-0.2 F{60*60} # Tiny retract at end Print 
      {% set z_move = [printer.toolhead.axis_maximum.z, printer.toolhead.position.z+4] | min  %} # Hop
      G1 X40 Z{z_move} E-0.8 F{60*400} # Print end retract 

      #Tip Forming and Filament Park
      {% if client.my_end_retract > 0 %}
        G1 E-{(client.my_end_retract)*0.5} F{10*60}
        G1 E{(client.my_end_retract)*0.5} F{80*60}
        G1 E-{(client.my_end_retract)} F{10*80}
      {% endif %}
    {% endif %}
 
    RESPOND TYPE=command MSG='Print Ended! Turning things off.'
    
    {% if rt.automeshed == True %}  # Clear Adaptive Bed Mesh
      BED_MESH_CLEAR
    {% endif %}

    {% if rt.offset_applied == True %}  # Clear offset
      SET_GCODE_OFFSET Z_ADJUST= -{client.smooth_plate_offset}
      SET_GCODE_VARIABLE MACRO=_CLIENT_VARIABLE_RUNTIME VARIABLE=offset_applied VALUE=False
      RESPOND TYPE=command MSG='Cleared smooth plate offset!.'
    {% endif %}

    SET_GCODE_VARIABLE MACRO=_CLIENT_VARIABLE_RUNTIME VARIABLE=start_change VALUE=False
    

    G90 # Absolute positioning
    {% if rt.end_park == False %}
      _TOOLHEAD_PARK_PAUSE_CANCEL
      SET_GCODE_VARIABLE MACRO=_CLIENT_VARIABLE_RUNTIME VARIABLE=end_park VALUE=True
    {% endif %}
    Qmode_exit
    OFF

    {% if client.stop_bg_services == True %}
      _START_CRON  # Enable background host scheduled tasks
    {% endif %}
    
    M117 Done!



[gcode_macro OFF]
gcode:
    {% set client = printer['gcode_macro _CLIENT_VARIABLE'] %}
    M84                                  # turn steppers off
    TURN_OFF_HEATERS                     # turn bed / hotend off
    M107                                 # turn fans off
    M106.1 S0                            # force part fan off
    {% if client.has_aux_fan == True %}  # force aux fan off
      SET_FAN_SPEED FAN=aux SPEED=0
    {% endif %}
    #SET_FAN_SPEED FAN=Exhaust SPEED=0   # turn exhaust fan off
    #SET_FAN_SPEED FAN=BedFans SPEED=0   # bed fan off
    #SET_PIN PIN=caselight VALUE=0       # turn case light off
    RESPOND TYPE=command MSG='All OFF'



[gcode_macro M109] # Wait Hotend Temp
rename_existing: M109.1
gcode:
    {% set s = params.S|float %}
    {% set range = printer['gcode_macro _CLIENT_VARIABLE'].heat_range if printer['gcode_macro _CLIENT_VARIABLE'].heat_range is defined else 5 %}
    
    M104 {% for p in params %}{'%s%s' % (p, params[p])}{% endfor %}  # Set hotend temp
    {% if s != 0 %}
        TEMPERATURE_WAIT SENSOR=extruder MINIMUM={s-range} MAXIMUM={s+range}   # Wait for hotend temp (within n degrees)
    {% endif %}



[gcode_macro M190] # Wait Bed Temp
rename_existing: M190.1
gcode:
    {% set s = params.S|float %}
    {% set range = printer['gcode_macro _CLIENT_VARIABLE'].heat_range if printer['gcode_macro _CLIENT_VARIABLE'].heat_range is defined else 5 %}

    M140 {% for p in params %}{'%s%s' % (p, params[p])}{% endfor %}   # Set bed temp
    {% if s != 0 %}
        TEMPERATURE_WAIT SENSOR=heater_bed MINIMUM={s-range} MAXIMUM={s+range}  # Wait for bed temp (within n degrees)
    {% endif %}


    
[gcode_macro _PURGE_LINE] # Purge line
gcode:
    {% set client = printer['gcode_macro _CLIENT_VARIABLE'] %}
    G90 
    M83
    G0 X{client.purge_x} Y{client.purge_y} Z{client.purge_z} F12000
    G1 E{client.my_end_retract} F500
    G1 X{client.purge_x+client.purge_length} Y{client.purge_y} E{0.2*client.purge_amount} F500
    G1 X{client.purge_x+client.purge_length+15} E-0.01 F1000
    G1 Y{client.purge_y+30} Z{client.purge_z+10} E-0.01 F18000 
    


#### Quiet Modes #####
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

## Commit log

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2023-10-01 Created Mount for Manta M8P
    A mount for BTT Manta M8P. Removes the need for separate RPi and 48V capable.
    [Mount Manta M8P.stl]
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2023-10-01 Added Mount Manta M8P (#1)
    * Created Mount for Manta M8P
    * Upload Manta M8P Mount
    * Add BOM Screws Cart
    * Manta M8P Mount CAD files
    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
    [Mount Manta M8P.stl, Mount Octopus Pro.stl]
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2023-10-01 moving Manta M8P STL and creating an Extras folder for other addons/optional components
    [Mount Manta M8P.stl]
2023-10-02 Changing f3d merged version to f3z for easier modding and export. Adding 200 bed straing releif. Cleanup
    [Breakout Box.f3z]
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2023-10-15 Fix Klipper Macro typo
    [mymacros.cfg]
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2023-10-16 Changing Ebox fan to Controller_fan tied to stepper Y# Please enter the commit message for your changes. Lines starting
    [mymacros.cfg, printer.cfg]
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2023-10-16 Shortening ebox idle fan durration
    [printer.cfg]
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2023-10-18 Updating the parts with guide tabs to fit in extrusions with 8mm gaps
    [AC Z LimitStop Down Right.stl, AC Z LimitStop Mount Down Left .stl, Other Parts.3mf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]
2023-10-21 Adding Polyimide Flex PCB Heater Design
    [HeatedBedFoil-B_Mask.gbr, HeatedBedFoil-Edge_Cuts.gbr, HeatedBedFoil-F_Cu.gbr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]
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2023-10-23 Updating missing counter bore on Y B mount. Small tolerance updates on X mounts to accomodate different screws, and a tighter fit with the X extrusion.
    [AC X Mount Left SUP.stl, AC X Mount Right SUP.stl, AC Y Stepper Mount B x2 .stl]
2023-10-24 Updating Flex Stiffener information.
    [HeatedBedFoil.kicad_pcb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]
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2023-10-29 Changing Toolhead Tensioner tolerances for easier belt insertion. Fixing the alignment of a hex key hole for the Z Tensioner Base
    [Toolhead Tensioner.stl, Z Tensioner Base Left.stl, Z Tensioner Base Right.stl]
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2023-11-08 Adding NF Crazy - Reverse Block Cutout - Toolhead
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2023-11-10 Fixing missing bevel
    [AC X Mount Left SUP.stl]
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2023-11-12 README.md - Fixing reversed CAD Preview links
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2023-12-16 Updated the X tensioner. Minor tolerance updates for the X mounts.
    [Toolhead Tensioner.stl]
2023-12-17 tolerance changes to the Y belt tool and Y tensioner plate
    [Other Parts.3mf, Y Belt Set and Tension Tool.stl, Y Belt Tensioner Plate.stl]
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2023-12-23 Adding Reverse Bowden Coupler
    [Bowden Coupler M10.step, Bowden Coupler M10.stl]
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2024-01-04 Adding reverse bowden coupler arm
    [Bowden Coupler M10 w Arm.step, Other Parts.3mf]
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2024-01-09 Fixing "X Mount Left" fitting issue with the X extrusion
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2024-01-18 Minor tolerance changes to Z motor mounts to allow for washers
    [Z Stepper Mount Left Base.stl, Z Stepper Mount Right Base.stl]
2024-01-18 Minot tolerance changes around the bearing insert area
    [AC Y Stepper Mount B x2 .stl]
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2024-01-18 Tolerance fixes to the X Insert Bearing Holder
    [X Bearing Insert.stl]
2024-01-19 fixing hidden octo mount
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2024-01-23 fixing aux fan screw size.
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2024-01-27 Removing the T-nut Spacer for the Y feet - the insertion is too frustrating.
    [T-nut 30 M5 Clamp.stl]
2024-01-29 fixing top panel orientation
    [Ebox Parts.3mf]
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2024-02-15 printer.cfg: fixing default hotend fan speed to 1.0
    [printer.cfg]
2024-02-16 Update LH Stinger 0.4.json fixing PRINT_START macro name
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2024-02-25 Major refactoring to the bundled macros focusded around the fan speed control and the quiet mode. Note: The PRINT_START macro was renamed to LHS. Please update the printer profiles.
    [KAMP_Settings.cfg, mymacros.cfg, printer.cfg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]
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2024-02-27 X mount changed to double shear shaft support for regular motor shaft sizes
    [X Bearing Insert.stl]
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2024-03-20 Fixing typo on silkscreen
    [LHS Breakbeat-B_Cu.gbr, LHS Breakbeat-B_Mask.gbr, LHS Breakbeat-B_Paste.gbr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]
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2024-03-20 Adding heater flex pcb image
2024-03-28 printer.cfg - fixing Aux fan Pin assignment
    [printer.cfg]
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2024-04-12 Disabled bed mesh fade Brought the ZTilt probe points closer to the center of the bed to avoid possible uneven or warped bed extremeties
    [quickdrawprobe.cfg]
2024-04-12 Reverted Minimum Sparse Infill Threadshold to 15
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2024-04-14 Fixing minor extrusion issue and increasing thickness of sherpa insert.
2024-04-14 Adding Y Mount mod based on MR105 bearings and a 9mm fixed pulley
    [AC Y Stepper Mount A Mod SUP x2.stl, AC Y Stepper Mount B Mod x2.stl]
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2024-04-19 Updating bearing tolerances
    [AC Y Stepper Mount A Mod SUP x2.stl, AC Y Stepper Mount B Mod x2.stl]
2024-04-19 Reinforced Sherpa Mini heat inserts areas
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2024-04-22 Adding Aux Fan UUHF Goliath version. Nozzle 13,6mm lower than the Dragon HF
    [Flap UUHF Goliath x2.stl]
2024-04-23 Removing SSR Cover (the BOM model doesn't require one)
    [Ebox Parts.3mf]
2024-04-23 - Smarter Load/Unload Filament Macros - Default temp set to 220C, or retain the current temperature target if no temperature specified and the current temperature is above 220 - Streamline Speed Cont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
    [mymacros.cfg]
2024-04-24 Adding missing grub screws for Three Way Corder
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2024-05-04 Moved the LSR-350 PSU by 3mm to make more room for the wiring. Raspberry PI might also be able to share the same BTT PI mount when powered though USB-C if using a 90 degree plug with a depth of 8mm.
    [Mount Pi (Rasp, BTT).stl, Panel Bottom.stl, Panel Left.stl]
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2024-05-06 adjusted machine bed origin offsets retractions reverted to conservative settings wipe_on_loops - disabled filament fixed accidental wipe overrides on some presets
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2024-05-06 - tweaked most coordinates related to probes/meshes, bed, screws, etc - removed KAMP requirements and usage - added klipper's native adaptive meshing to the PRINT_START_LHS macro - replaced KAMP purg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
    [KAMP_Settings.cfg, mymacros.cfg, printer.cfg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]
2024-05-08 chube: fixing M3 mounting screw tolerances
    [Toolhead Chube Air Orbiter.step, Toolhead Chube Air Sherpa Mini.step]
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2024-05-09 fixing heater block clearance and various minor tweaks
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2024-05-15 changing to 4 perimeters for better overhang performance due to slicer issues
    [Aux Fan Parts.3mf]
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2024-05-23 label fixes
    [Cable Labels.3mf]
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2024-05-23 fixing missing counterbore bridge on ebox foot
    [Foot x4.stl]
2024-05-23 mymacros.cfg: - added user variables for nozzle heat position and M600 filament change - added user variables for PRINT START moves velocity and acceleration - lowerer heat and wait threshold to -3C 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
    quickdrawprobe.cfg:
    - lowered zhop to 12
    [mymacros.cfg, quickdrawprobe.cfg]
2024-05-25 fixing Qmode velocity caps not being set
    [mymacros.cfg]
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2024-05-26 fixing fan speed rounding issue and adding prompts to filament macros
    [mymacros.cfg]
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2024-05-29 small geometry fix on AC Toolhead Trim
    [AC Toolhead Trim.stl]
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2024-06-06 fixed typo in has_aux_fan and updated instructions
    [mymacros.cfg]
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2024-06-14 fixing wrong wiring harness fan connectors pinout (reversed polarity)
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2024-06-14 ebox: cable guide low-large features two mounting screws cable port trim has a mating feature with the cable port A piece
    [AC Cable Port Trim.stl, Cable Port A.stl, Panel Bottom.stl]
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2024-06-15 increasing tolerances and adding extra mounting features
    - Added heat inserts for fan mounting
    - Magnet holes tolerances increased
    - Added an extra screw mount to the lower cable guide to prevent from bending
    - Added an extra hole for mounting the smaller 48V PSU
    - Added indexing feature for the back cable hole piece and trim
    [Door Main.stl, Magnet Base Left.stl, Magnet Base Right.stl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]
2024-06-17 tweaking tolerances on the belt tool
    [Other Parts.3mf, Y Belt Tool Main.stl, Y Belt Tool Slider.stl]
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2024-06-21 fixed example code
    [testspeed.cfg]
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2024-06-25 aux fan screw hole tolerance fix
    [Aux Fan Parts.3mf, Flap UHF x2.stl, Flap UUHF Goliath x2.stl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]
2024-06-30 updating tolerances and adding standard variant
    [Flap UHF Thicker Fan x2.stl, Flap UHF Thicker Fan.step, Flap UHF for Thicker Fan x2.stl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]
2024-07-02 adding missing chamfer for countersunk screw and t-nut retainer clips
    [Breakout Box Parts.3mf, Breakout Main Body.stl]
2024-07-04 tolerance tweaks and removing a screw hole and a double sided pin
    [Breakout Box Parts.3mf, Breakout Top Plate.stl]
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2024-07-04 changed aux flap printing orientation and added support to the Orca files renamed aux flaps as support required parts set 100% infill for the small tensioner parts
    [Aux Fan Parts.3mf, Flap SUP x2.stl, Flap UHF SUP x2.stl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]
2024-07-04 removing one t-nut for ease of installation and increasing access to the bed cable connector
    [Breakout Box Parts.3mf, Breakout Main Body.stl, Breakout Standoff Single x2.stl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]
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2024-07-15 adding clearance for AGND connector
    [Breakout Box Parts.3mf, Breakout Top Plate.stl]
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2024-07-20 thermistor wiring fix for BTT boards - JST pins on the mainboard side were flipped
2024-07-21 fixing hotend fan screw hole offset
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2024-07-21 increased X inner tensioner block height for tighter grip
    [AC Toolhead Tensioner Inner.stl]
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2024-07-23 lowering Z belt clamp tolerances
    [AWD X.3mf]
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2024-07-25 added comments indication not to change position_endstop and position_min for X/Y axis
    [printer.cfg]
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2024-07-29 optimized board position for better driver airflow - board was shifted to the left
    [FYSETC Spider V3 Mount.step, FYSETC Spider V3 Mount.stl]
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2024-08-03 adding stop_bg_services (default: false) option to stop host scheduled tasks during print
    [mymacros.cfg]
2024-08-03 fixing Z Tilt horizontal move
    [mymacros.cfg]
2024-08-04 fixing adc conversion values for tmc warning registries
    [steppers.cfg, steppersfast.cfg]
2024-08-06 updating PRINT_END do fix a potential out of range situation
    [mymacros.cfg]
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2024-08-09 - added (commented) MPC filament gcode settings for danger klipper - increased PLA temps from 225 to 230 (increase with volumetric flow if not using MPC) - tweaked PETG filament profile - adding PETG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
2024-08-10 fix wrong filament gcode comment symbol
2024-08-10 fixing end Z move
    [mymacros.cfg]
2024-08-10 updating tolerances and adding indexing features
    [AC X Mount Left - Ext Z - SUP.step, External Z Belt Clamp.stl]
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2024-08-11 lowering Y cart mount screw tolerances
    [Y Cart Mount x2.stl]
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2024-08-18 v1.01: changing copper weight to 2oz, adding xt30 cutout, various tolerance updates
    [LHS Breakbeat-B_Cu.gbr, LHS Breakbeat-B_Mask.gbr, LHS Breakbeat-B_Paste.gbr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]
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2024-08-20 adding quantities for xN parts, and removing parts found in user mods
    [3030 Cable Clamp 90D x6.stl, 3030 Cable Clamp x6.stl, 3030 Slot Cover Long x4.stl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]
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2024-08-21 fixing stl naming typos
    [AWD X Bearing Insert Right.stl, Bottom Bracket.stl, LH-Stinger_Fan_Grill-LED-Diffuser.stl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]
2024-08-22 fixed coupler thread dimensions
    [Bowden Coupler M10.stl]
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2024-08-22 explicitly defining extruder speed limits due to possibly wrong klipper default value calculations
    [printer.cfg]
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2024-08-25 increasing the tolerance of the X Toolhead Tensioner block
    [Toolhead Tensioner.stl]
2024-08-25 updating endstop tolerances to allow for a larger range of microswitches
    [Y Endstop.stl, Z Endstop - UUHF (Goliath) Hotends.stl, Z Endstop UUHF (Goliath) Hotends.step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]
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2024-08-28 updating Z drives to use the same bearing clamp and decreasing bearing tolerances
    [Z Stepper Mount Bearing Clamp x5.stl, Z Stepper Mount Left Base.stl, Z Stepper Mount Left Clamp A.stl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]
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2024-09-01 decreasing bottom part thickness to increase clearance against Y extrusion
    [AC Y Belt Clamp.stl]
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2024-09-04 adding a custom TPOWERDOWN setting of ~4.3 seconds along with 1A hold current for the HV steppers
    [steppers.cfg, steppersfast.cfg]
2024-09-05 correcting wrong fan orientation in preview image
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2024-09-06 improving AWD sync and FORCE_SET_POS to lock at full steps, prefixing NON-UI macros to for exclusion (_PURGE_LINE, _GO_....)
    [mymacros.cfg]
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2024-09-10 correcting extrusion length typo
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2024-09-10 increased tolerances and added a bump stop to avoid the possibility of pulleys rubbing on the X extrusion
    [X Bearing Insert.stl]
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2024-09-15 lowering nozzle pre-heat target to prevent oozing
    [mymacros.cfg]
2024-09-16 fixing issue with PURGE_LINE macro not being called at PRINT_START
    [mymacros.cfg]
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2024-09-18 adding note regarding the use of steppersfast.cfg and lowering max current to 1.9A
    [printer.cfg, steppersfast.cfg]
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2024-09-22 adding [bed mesh] faulty regions for screw avoidance
    [quickdrawprobe.cfg]
2024-09-25 fixing typo in max_extrude_cross value
    [printer.cfg]
2024-09-25 lowering Z position_min to avoid false trigger runout during docking stage
    [printer.cfg]
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2024-09-29 Adjusting tolerances
    [Fysetc Nozzle ADXL Bed Mount.step, Fysetc Nozzle ADXL Bed Mount.stl]
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2024-10-06 X tensioner block and tensioner inner piece update: raising belt entrance by 0.3mm for better alignemnt
    [AC Toolhead Tensioner Inner.stl, Toolhead Tensioner.stl]
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2024-10-24 taller roller rims and concave profile, adding attachment slot to mid section for future accesories
    [AC Mid.stl, AC Wheel x4.stl, Cage x4.stl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]
2024-10-26 minor tolerance updates for a few heat insert holes
    [Door Top.stl, Panel Right.stl, Panel Top.stl]
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2024-10-27 refactoring mymacros.cfg and splitting the variables from code base please port your settings to the new format
    [mymacros.cfg, mymacros_code.cfg]
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2024-10-27 fixing a collision with a backside component in the lower right screw mount
    [FYSETC Spider V3 Mount.step, FYSETC Spider V3 Mount.stl]
2024-10-28 fixed screw quantities
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2024-10-28 fixing version check
    [mymacros_code.cfg]
2024-10-28 fixing hub loading when filament preent and adding previously loaded filament purge when chaging lanes before the print start
    [sp_mmu_code.cfg]
2024-11-23 Increrasing tolerances of the Cable Clamps
    [3030 Cable Clamp 90D x6.stl, 3030 Cable Clamp x6.stl]
2024-11-25 fixing BOM motor specs
2024-11-27 decreasing tolerances for the X inner tensioner piece for ease of installation
    [AC Toolhead Tensioner Inner.stl]
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2024-12-07 fixing SP_TEST_MMU
    [sp_mmu_code.cfg]
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2024-12-07 updating adxl configs for the new sweeping vibrations resonance testing
    [adxl.cfg]
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2024-12-09 fixing end_of_load_filament_move
    [sp_mmu_code.cfg]
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2024-12-11 fixing bom
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2024-12-14 improving PARK CENTER macro for better positioning and workflow during the z_offset adjustment procedure
    [mymacros_code.cfg]
2024-12-14 setting first layer to rectilinear, adding brim and removing el foot compensation for better overhang fillets
    [Filament Hub O2.3mf]
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2024-12-17 updated code and configuration to v0.4 added support for different hub configurations fine tuned movement stages for non ideal setups various other fixes and improvements
    [sp_mmu.cfg, sp_mmu_code.cfg]
2024-12-17 small tweak of the tip shaping macro to compensate for the initial pause retract and adjusting the filament_park distance
    [sp_mmu.cfg]
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2024-12-17 fixing issue with RatOs client variables
    [sp_mmu_code.cfg]
2024-12-17 adding part variants with higher tolerances - marked with a dot
    [AC Toolhead Tensioner Inner - Tolerance ++.stl, AC Y Belt Tensioner - Tolerance ++.stl]
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2024-12-18 adding RatOS T0 conflict workaround
    [sp_mmu_code.cfg]
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2024-12-19 renaming SP_SET_EXIT_CODE and fixing default action for SP_UNLOAD_LANE
    [sp_mmu_code.cfg]
2024-12-19 tweaking default lengths, bringing synced move closer to sensor and reverting tip forming initial move from 1mm to 0.5mm
    [sp_mmu.cfg]
2024-12-20 tighter tolerances fitting with the O2 filament path
    [Filament Hub O2.3mf]
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2025-01-02 fixing park command
    [sp_mmu_code.cfg]
2025-01-03 fixing Z park speed
    [sp_mmu_code.cfg]
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2025-01-05 fixing Z restore position
    [sp_mmu_code.cfg]
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2025-01-07 updating part tolerances around the microswitch
    [Filament Hub O2.3mf]
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2025-01-17 v0.7 update - new guest lane implementation for 3+1 or 4+1 setups - new notification system for hooking up external devices - new slicer driven purge amounts for parked purges - new filament runout p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
    Please take your time and carefully migrate your old sp_mmu.cfg settings to the new format
    [sp_mmu.cfg, sp_mmu_code.cfg]
2025-01-18 lowering the hotend loading speed for the final stage aproaching the meltzone
    [sp_mmu_code.cfg]
2025-01-18 fixing qmode motion limits not being applied
    [mymacros_code.cfg]
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2025-01-25 fixing runout sensor not being enabled at print start under certain conditions
    [sp_mmu_code.cfg]
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2025-01-26 lowering homing speed to avoid loud motor resonances
    [quickdrawprobe.cfg]
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2025-01-30 fixing sp print start missing variable declaration
    [sp_mmu_code.cfg]
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2025-01-31 clearing user macro execution even if print start fails
    [sp_mmu_code.cfg]
2025-01-31 trying workaround for timer too close issue https://klipper.discourse.group/t/mcu-mmboard-shutdown-timer-too-close/376/2
    [sp_mmu_code.cfg]
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2025-02-06 fixing bom shaft unit
2025-02-07 adding flip stop cut
    [Flip Stop Cut.3mf]
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2025-02-07 adding user configurable heat range setting, and moving the bed the center at print start if Y is homed, to avoid heating over the motors
    [mymacros_code.cfg]
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2025-02-09 fixing print_start_change_purge variable from runout code
    [sp_mmu_code.cfg]
2025-02-09 chaging default Y position while waiting for hotent heating to avoid the bed sitting over the motor mounts
    [mymacros.cfg]
2025-02-09 resetting filament settings
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2025-02-13 improving skipping unloading hotend console message
    [sp_mmu_code.cfg]
2025-02-13 trying to catch SAVE_VARIABLE config issues
    [sp_mmu_code.cfg]
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2025-02-20 - Adding REFRESH_STATE calls thoughout the manual macros to obtain fresh sensor state - Adding NO_START_PURGE option to _SP_PRINT_START for custom purge setups - Disabling RESTORE_PA from triggering 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
    [sp_mmu_code.cfg]
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2025-02-26 fixing purging during infinite spool, adding messaging regarding purge amount
    [sp_mmu_code.cfg]
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2025-03-01 tweaking ECAS Hub tolerances
    [Filament Hubs.3mf]
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2025-03-04 fixing default temperature behaviour
    [brush.cfg]
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2025-03-07 inverting Z direction pins
    [printer.cfg]
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2025-03-07 fixing indent
    [sp_mmu_code.cfg]
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2025-03-09 fixing params logic in manual macro and enforcing params type casting
    [sp_mmu_code.cfg]
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2025-03-12 fixing filament change error when unload lane is empty
    [sp_mmu_code.cfg]
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2025-03-24 - changing saved variable detection at boot for better behaviour when config not preset - fixing SP_FORCE_SET_LOADED_LANE hotend loaded variable - adding support for Kalico non linear pressure advanc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
    [sp_mmu_code.cfg]
2025-03-26 removing shorter shafts from bom listing
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2025-04-02 adding missing variable_lane_em placeholder for the 4th lane
    [sp_mmu.cfg]
2025-04-03 reverting tip forming cooldown distance to 5mm and lowering meltzone loading speed to 10mm/s
    [sp_mmu.cfg]
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2025-04-03 fixing retract move for legacy sync method
    [sp_mmu_code.cfg]
2025-04-03 fixing legacy mode
    [sp_mmu_code.cfg]
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2025-05-06 adding dummy dwell for people with soft filament in extruder issues
    [sp_mmu.cfg]
2025-05-16 increasing tilt retry tolerance by 0.005
    [mymacros_code.cfg, quickdrawprobe.cfg]
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2025-06-01 Adding Hammer Stop Cut by @Dan329 and removing Flip variant
    [Flip Stop Cut.3mf, Hammer Stop Cut.3mf]
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2025-06-03 adding skip_first_park advance option - 1/0 - disable the first parking move when using filament cutters which take over that task
    [sp_mmu.cfg, sp_mmu_code.cfg]
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2025-06-08 fixing speed variable and adding Y move
    [sp_mmu.cfg]
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2025-06-08 Chaging resume position restore speed to park_speed. Adding Z parking move during pause for skip_first_park=1
    [sp_mmu_code.cfg]
2025-06-08 adding short action stopper
    [Orbiter - Sherpa - Filament Cutter.3mf]
2025-06-13 RatOS: SP_CHANGE was renamed to _SP_CHANGE to avoid misuse - please update your slicer g-code
    [sp_mmu.cfg, sp_mmu_code.cfg]
2025-06-19 Updating X tensioner block to avoid layer separation on block insertion
    [Toolhead Tensioner.stl]
2025-06-22 adding SP_TEST_SERVO angle error message description
    [sp_mmu_code.cfg]
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2025-08-11 fixing screw hole location
    [RPI 90Deg Mount.step, RPI 90deg Mount.stl]
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2025-08-19 Increasing tolerances to aid easier hotend insertion and updating instructions
    [Goliath_AUX_Aero_Diverter.step, Goliath_AUX_Aero_Diverter.stl, Goliath_Chube_AUX_Aero_Diverter.step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]
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2025-08-30 Adding Orbiter - Flipped direction cutter body
    [Orbiter - Flipped Cut Direction .step]
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2025-09-08 fixing link to sensor assembly
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2025-09-30 Chaging default to variable_legacy_klipper: 1 due to latest klipper issues. Should help people on first set-up
    [sp_mmu.cfg, sp_mmu.cfg-for-LH-Stinger-Fysetc Kit.cfg]
2025-09-30 updading sync mode error msg visiblity
    [sp_mmu_code.cfg]
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2025-12-09 Fix: Z hop park move not triggered when using skip_first_park Change: An additional sync move is performed when the filament unload failed to clear the sensor Change: Succesive guest lane changes are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
    [sp_mmu_code.cfg]
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2025-12-18 tweaking rear wiring tolerances - @Wight554
    [Toolhead Chube Air Orbiter.step, Toolhead Chube Air Sherpa Mini.step]
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2026-01-05 removing left side screw due to potential collision with the motor mount
    [Goliath_Chube_AUX_Aero_Diverter.step, Goliath_Chube_AUX_Aero_Diverter.stl, UHF_AUX_Aero_Diverter.step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]
2026-01-07 trying workaround for "must unregister axis first"
    [sp_mmu_code.cfg]
2026-03-13 Fix STOP_ON_ENDSTOP deprecated warning
    [sp_mmu_code.cfg]
2026-04-14 ### VERSION: 1.0.4
    - Breaking Change: CONFIGURATION TEMPLATE VERSION: 0.9.4 -- This means that you have to port the differences to your existing config
    Changes:
    - Introduced two new advanced options:
    variable_retrigger_guest_lane: 0 # 1/0 controls if successive guest lane changes trigger a lane change
    variable_legacy_endstop_msg: 0 # 1/0 changes manual stepper stop message type. Use 1 only for sync_mode 2 with early klipper v0.13.0 versions.
    The legacy_endstop_msg varible was added due to klipper API changes on manual stepper stop type.
    Flip this variable if you get errors related to manual stepper endstop type.
    - _SP_PRINT_START now sets a "fuse" variable for the tool chan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
    [sp_mmu.cfg, sp_mmu_code.cfg]
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
